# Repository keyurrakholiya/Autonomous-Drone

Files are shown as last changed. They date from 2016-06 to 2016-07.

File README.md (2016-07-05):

e-Yantra Summer Internship
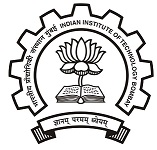
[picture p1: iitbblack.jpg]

***
# eYSIP-2016-Autonomous-Drone
Through this project we want to make an Autonomous Drone that can travel from one point to another based on its GPS Location. This drone can be used for tracking objects and aerial photography when interfaced with an Object Tracking Camera system.

Autonomous Drone project uses the following components:
* **Flight Controller:** Ardupilot Flight Controller (APM 2.6)
* **Copter Firmware:** v3.2.1
* **Communication Protocol:** MAVLink, MAVProxy, UART
* **Ground Station System (Software):** Mission Planner v1.3.30
* **Programming Language:** (Python 2.7)
* **Companion Computer:** Raspberry Pi B+ model

##Description:
***
The latest technology currently in markets is the Drone Technology, Drones can solve a lot of purposes such as security & surveillance, mapping unreachable or hard to reach sites, aerial photography, military purposes, forest survey, etc. So, we have created a drone which is completely autonomous as well as it can be manually controlled with laptop using remote login.

##Features:
***
- **Auto Take-off and Land:** The Drone can automatically take-off to a desired height, wait at that height for a predetermined time and then land.
- **Manual control using remote-login:** User can manually control the drone using the keyboard keystrokes of the laptop using remote login with raspberry pi.
- **Autonomous flight between multiple points:** The drone can autonomously take-off complete a mission and land either at the start position or your desired position. A mission is a set of locations where you want your drone to go. The drone gets the locations from the GPS module interfaced with the APM board.
- **Indoor auto take-off and land using ultrasonic sensor:** The drone also has an Ultrasonic sensor interfaced with Raspberry Pi which can be used for take-off and land indoors, where the altitude the drone needs to reach is just few meters.
- **Failsafe:** The APM has smart failsafe features which include low battery voltage failsafe, remote signal lost. So, with these failsafe features you can either put your drone into landing mode or else if you have a GPS module you can even have Return To Launch feature and also many more options are provided.

##Key Tasks
***
* Calculations for selecting motors, propellors, flight controller, battery for a Quadcopter
* Building and assembling the drone
* Stabilizing the drone for manual as well as autonomous control
* Interfacing Raspberry Pi with APM  flight controller
* Develop python codes to achive autonomous behaviour of drone

##Deliverables
***
* An Autonomous Drone
* Code and Documentation
* Tutorials explaining individual modules

##Documentation
***
* Detailed tutorials with actual component pictures on every module of the project have been uploaded on GitHub.

##Contributors
***
  * [Akshit Gandhi](https://github.com/akshitgandhi)
  * [Keyur Rakholiya](https://github.com/keyurrakholiya)
  
## Mentors
***
  * Pushkar Raj
  * Akshat Jain
  * Rama Kumar

##License
***
This project is open-sourced under [MIT License](http://opensource.org/licenses/MIT)

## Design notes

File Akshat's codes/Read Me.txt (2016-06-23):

These are the codes I used during my quadcopter project. 

Please do not attempt to run the codes directly as they will give errors. Make sure all the libraries used in the codes are installed on your device.

P.S.: Remove lines that are not relevant to you else it will give errors.

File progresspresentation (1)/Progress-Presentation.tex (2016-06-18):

\documentclass[10pt, a4paper]{beamer}

\usetheme{Berkeley}
\usecolortheme{sidebartab}

\documentclass{article}
\usepackage{graphicx}

\begin{document}
	\setbeamertemplate{sidebar left}{}
	\title{Progress Presentation-I}
	\subtitle{e-Yantra Summer Intership-2016 \\ $Autonomous-Drone$}
	\author{Akshit Gandhi\\Keyur Rakholiya\\
	Mentors:\\ Pushkar Raj\\Akshat Jain\\Rama Kumar}
	\institute{IIT Bombay}
	\date{\today}
	%\addtobeamertemplate{sidebar left}{}{\includegraphics[scale = 0.3]{logowithtext.png}}
	\frame{\titlepage}

\setbeamertemplate{sidebar left}[sidebar theme]
\section{Overview of Project}
\begin{frame}{Overview of Project}
	\textbf{Autonomous-Drone} \\
	\begin{itemize}
		\item Objective:\\
		            “Making an Autonomous Drone that can travel from one point to another based on its GPS Location. This drone can be used for tracking objects and aerial photography when interfaced with an Object Tracking Camera system.”

		\item Deliverables:\\
	1. An Autonomous Drone\\
2. Code and Documentation\\
3.Tutorials explaining individual modules

	\end{itemize}
\end{frame}

\section{Overview of Task}
\begin{frame}{Overview of Task}
\textbf{Task list}
 	\hspace{0.45in}\\
 	\begin{tabular}{|c|c|}
 		\hline
 		Task & Deadline &
 		\hline
 		Calculations for making a Quadcopter & 3/6/16 &
 		\hline
 		Calibrating APM & 5/6/16 &
 		\hline
 		Assembling the quad for manual flight & 7/6/16 &
 		\hline
 		Interface Gps with APM & 9/6/16 &
 		\hline
 		Interface Raspberry-Pi with APM & 11/6/16 &
 		\hline
 		Manual flight using R-pi & 15/6/16 &
 		\hline
 		Auto take-off and land using R-pi & 19/6/16 &
 		\hline
 		Create a flight planning algorithm & 25/6/16 &
 		\hline
 		Autonomous Flight & 3/7/16 &
 		\hline
\end{tabular}
\end{frame}

\section{Task Accomplished}
\begin{frame}{Task Accomplished}
	\begin{itemize}
	    \item Research on drone project.
		\item Assembly of drone.
		\item Understanding software and Flight controller features.
		\item Interface GPS.
		\item TEST FLIGHT-1 done.
		\item Research on dronekit Library version.
		\item Installing Rasbarian linux on R pi.
		\item connect R-pi to Ardupilot via USART or USB
		\item Run python code on R pi to get data from Flight controller.
	\end{itemize}
\end{frame}

\begin{frame}{Images}
	Quadcopter with Mission planer software: \\
	\centering
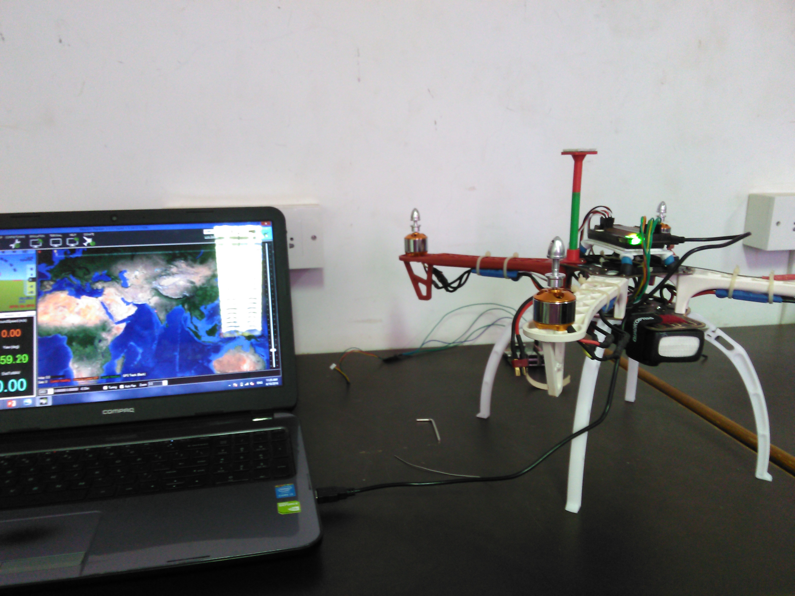
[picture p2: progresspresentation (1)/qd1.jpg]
		

\end{frame}

\begin{frame}{Images}
	Ardupilot Flight Controller: \\
	    \centering
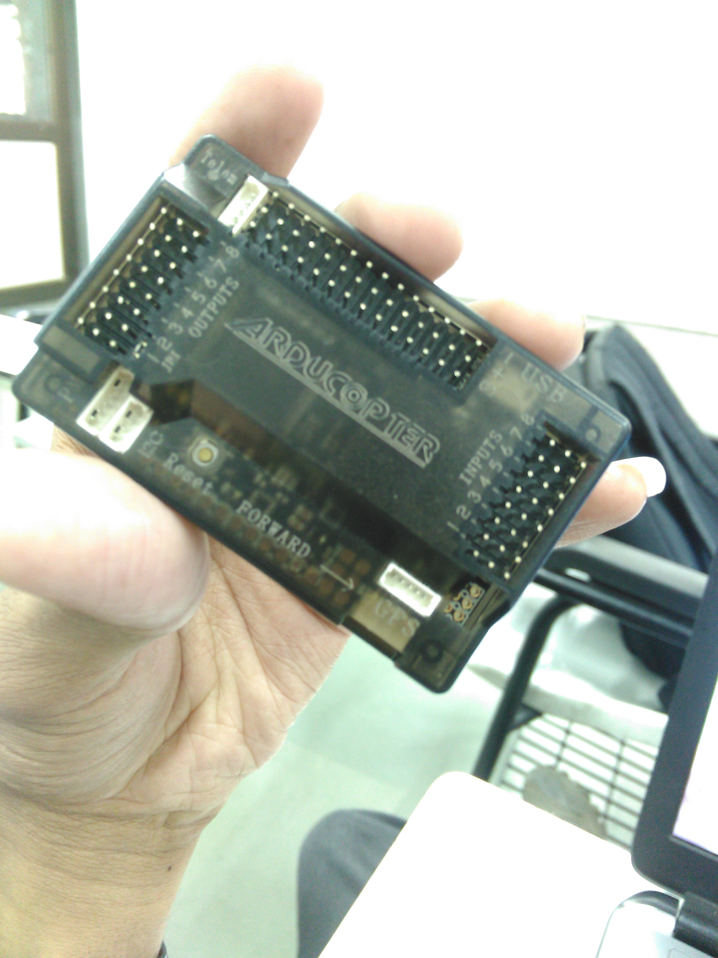
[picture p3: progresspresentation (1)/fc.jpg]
		
\end{frame}

\section{Challenges Faced}
\begin{frame}{Challenges Faced}
     \large\textbf{Hardware challenges}
	\begin{itemize}
	    \item Calculation of total approx weight.
	    \item For lifting the drone, calculate the thrust
	    \item knowing the aerodynamics rules
	    \item Choose the right propellers in size and pitch
	    \item Calculate flight time
	    \item BLDC motor power rating and KVA rating
	    \item Choose right battery 
	    \item Carbon fiber frame for drone
	    \inem Interfacing sensors Like GPS,SONAR
	    
	\end{itemize}
\end{frame}

\section{Challenges Faced}
\begin{frame}{Challenges Faced}
     \large\textbf{Software challenges}
	\begin{itemize}
	    \item Ardupilot is open source Hardware.They release new version after fixing bugs! its very difficult to choose right firmware  for your hardware among hundreds of software
	    \item Finding out suitable version of MISSION PLANNER for your firmware
	    \item More then 239 parameters are there. according to our mission we have to make changes
		\item Calibration axis of gyro and radio channels.
	\end{itemize}
\end{frame}

\section{Future Plans}
\begin{frame}{Future Plans}
	\begin{itemize}
	    
		\item Writing code in python 
		\item Making drone autonomous\\
		By Autonomous, we mean that drone will fly and reach to our desire destination without Remote control.
		\item Mounting camera on drone , and making it object tracking drone
	\end{itemize}
\end{frame}

\section{Thank You}
\begin{frame}{Thank You}
	\centering THANK YOU !!!
\end{frame}
\end{document}

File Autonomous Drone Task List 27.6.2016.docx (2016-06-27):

eYSIP – 2016

Autonomous Drone

Completed, Under Review and Upcoming Tasks as of 27/6/2016

Completed:

1. Calculations for deciding the components to be used for drone.
2. Assembly of Drone.
3. Calibrating APM.
4. First Manual Test Flight
5. Interfacing GPS with APM and reading values from it.
6. Interfacing Ultrasonic Sensor with APM and reading values from it.
7. Setting up the Raspberry Pi.
8. Create a Power distribution system for the drone, RPi and APM.
9. Interfacing the Raspberry Pi with APM.
10. Manual flight using Raspberry Pi (remote login). No need to prepare a tutorial for this but the code should be well commented.
11. Auto take-off and landing using Raspberry Pi.

Under Review:

1. Preparing a tutorial on “How to decide what parts to use for building a quadcopter?”
2. Tutorial on “Setting up your APM, calibrating all devices”.
3. Prepare a tutorial on interfacing the GPS with APM.
4. Prepare a tutorial on Power distribution system.
5. Prepare a tutorial on interfacing the Raspberry Pi with APM.

Upcoming:

6. Prepare a tutorial on interfacing the Ultrasonic Sensor with APM.
7. Commenting the “Manual flight using Raspberry Pi” code.
8. Commenting the “Auto take-off and landing using Raspberry Pi” code.
9. Designing of Path Planning Algorithm to travel from one GPS location to another. Prepare a tutorial for the same.
10. First Completely Autonomous Test Flight.
11. Debugging.
12. Adding features. Prepare tutorials if required.

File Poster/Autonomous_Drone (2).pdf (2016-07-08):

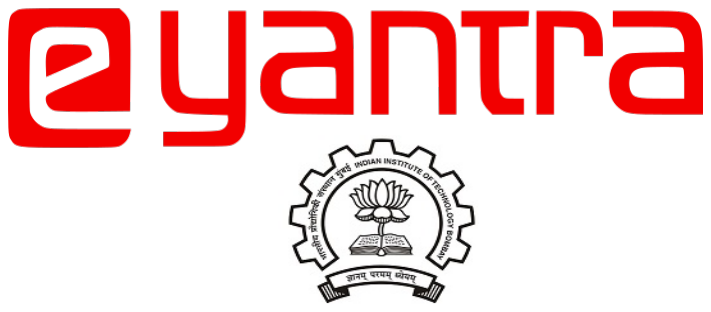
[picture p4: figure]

# Autonomous-Drone

Akshit Gandhi, Keyur Rakholiya. Mentors: Pushkar Raj,
Rama Kumar,
Akshat Jain.

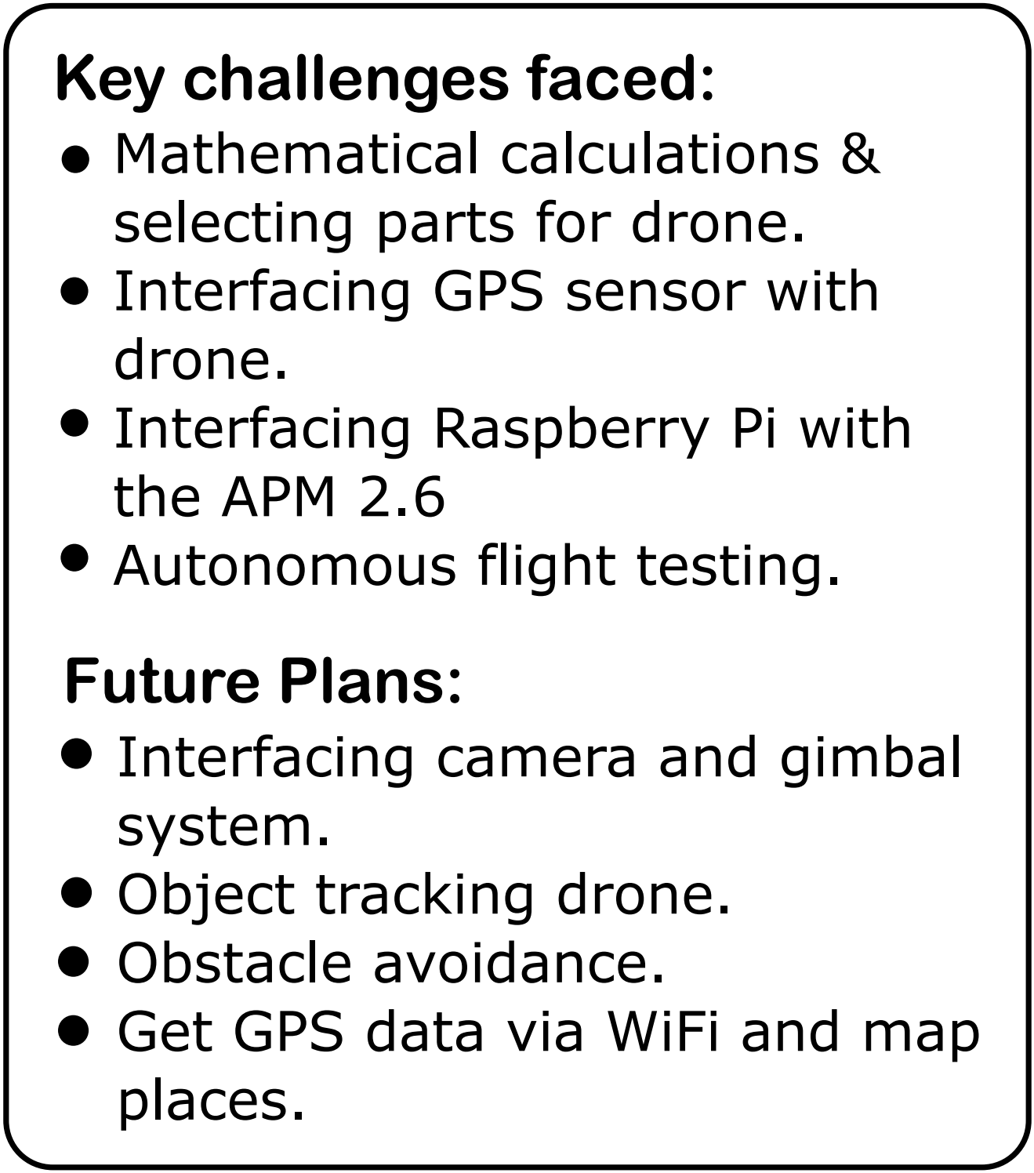
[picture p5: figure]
Key challenges faced: Mathematical calculations & selecting parts for drone. Interfacing GPS sensor with drone. Interfacing Raspberry Pi with the APM 2.6 Autonomous flight testing.; Future Plans: Interfacing camera and gimbal system. Object tracking drone. Obstacle avoidance. Get GPS data via WiFi and map places.
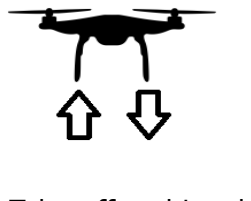
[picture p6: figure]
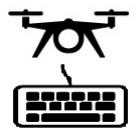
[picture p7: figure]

### e-Yantra Summer Internship Project 2016

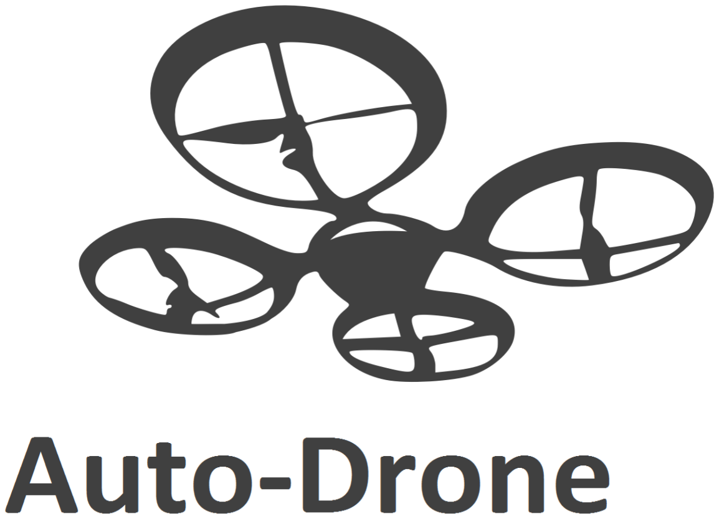
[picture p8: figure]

The latest innovation in the aviation industry is the Drone Technology.

### But, the drones that require manual input are very susceptible to radio inter-

ference or radio connection losses and they also have very limited features.

### So, we came up with a solution i.e the Autonomous-Drone

### Key Features:

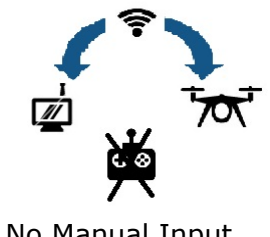
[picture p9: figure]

No Manual Input | Auto Take-off and Land | Control from keyboard

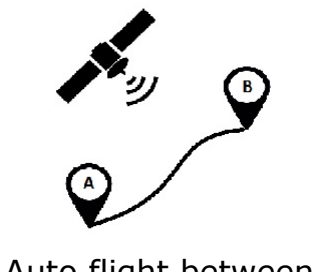
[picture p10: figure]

Auto flight between
multiple way-points

Indoor Take-off and land
with ultrasonic-sensor

Application fields include security surveillance, perimeter defence, mapping hard to reach sites, aerial photography, forest surveys, just to name a few!!

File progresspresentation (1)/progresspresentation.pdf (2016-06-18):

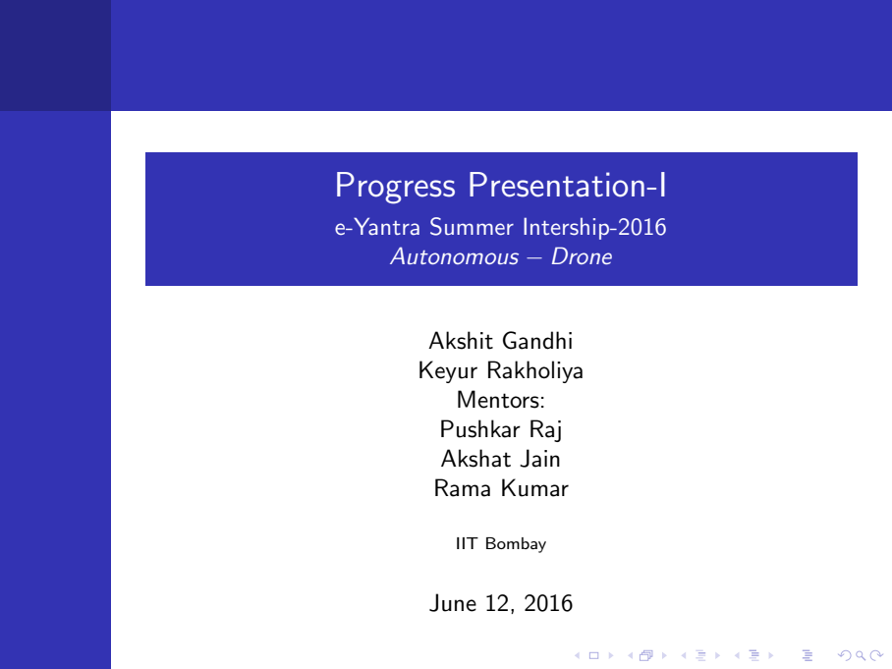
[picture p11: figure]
Progress Presentation-I; e-Yantra Summer Intership-2016 Autonomous − Drone; Akshit Gandhi Keyur Rakholiya Mentors: Pushkar Raj Akshat Jain Rama Kumar; IIT Bombay; June 12, 2016

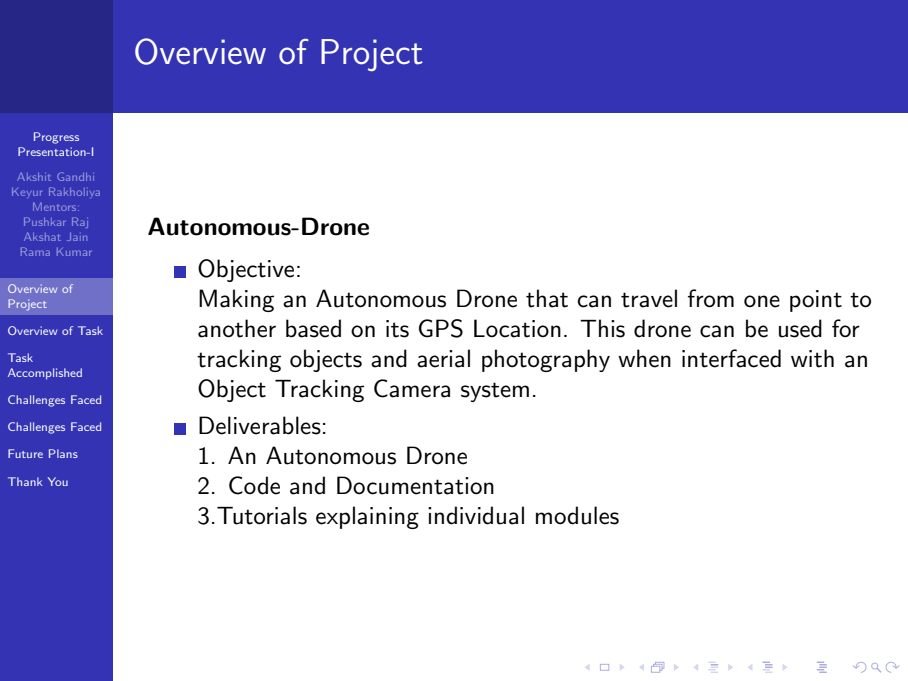
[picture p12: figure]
Progress Presentation-I; Akshit Gandhi Keyur Rakholiya Mentors: Pushkar Raj Akshat Jain Rama Kumar; Overview of Project; Overview of Task; Task Accomplished; Challenges Faced; Future Plans; Thank You; Autonomous-Drone; Objective:; Object Tracking Camera system.; Deliverables: 1. An Autonomous Drone 2. Code and Documentation

# Making an Autonomous Drone that can travel from one point to another based on its GPS Location. This drone can be used for tracking objects and aerial photography when interfaced with an

# 3.Tutorials explaining individual modules

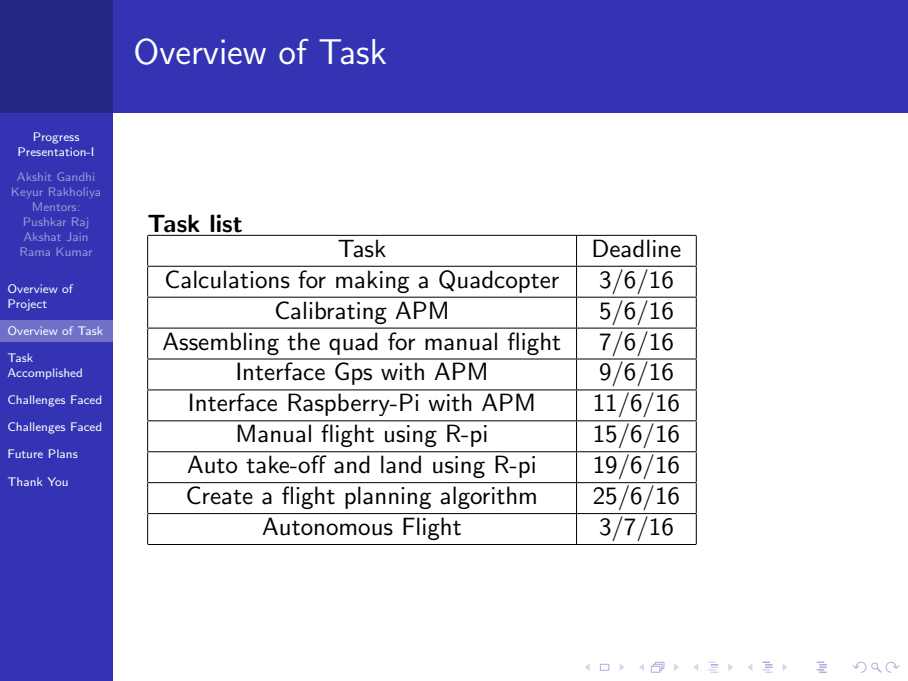
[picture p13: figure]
Progress Presentation-I; Akshit Gandhi Keyur Rakholiya Mentors: Pushkar Raj Akshat Jain Rama Kumar; Overview of Project; Overview of Task; Task Accomplished; Challenges Faced; Future Plans; Thank You; Task list; Task; Deadline; Calibrating APM; Interface Gps with APM; Interface Raspberry-Pi with APM; Manual flight using R-pi; Autonomous Flight

Calculations for making a Quadcopter | 3/6/16
Assembling the quad for manual flight | 7/6/16
Auto take-off and land using R-pi | 19/6/16
Create a flight planning algorithm | 25/6/16

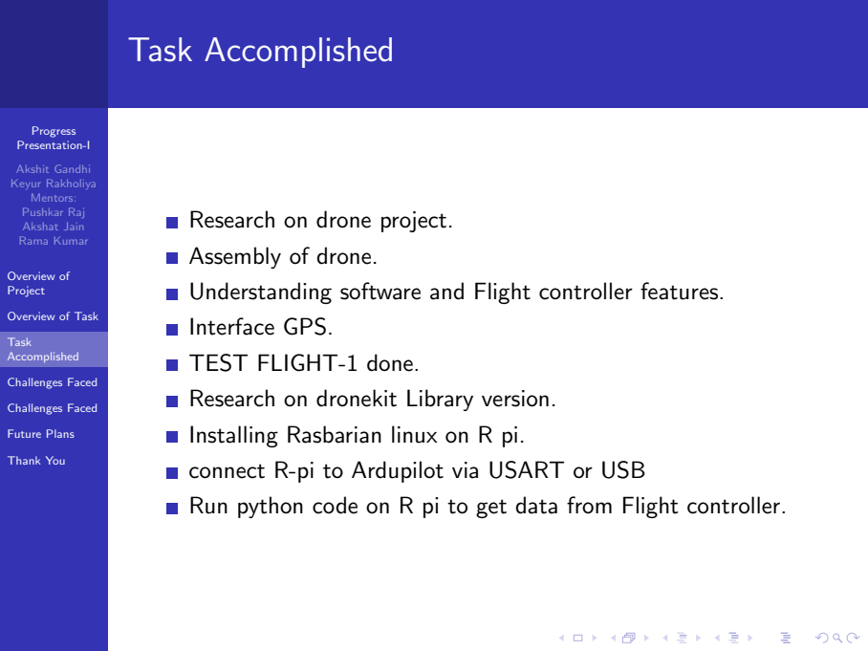
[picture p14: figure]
Progress Presentation-I; Akshit Gandhi Keyur Rakholiya Mentors: Pushkar Raj Akshat Jain Rama Kumar; Overview of Project; Overview of Task; Task Accomplished; Challenges Faced; Future Plans; Thank You; Research on drone project.; Assembly of drone.; Interface GPS.; TEST FLIGHT-1 done.; Research on dronekit Library version.; Installing Rasbarian linux on R pi.

Understanding software and Flight controller features.

# connect R-pi to Ardupilot via USART or USB

Run python code on R pi to get data from Flight controller.

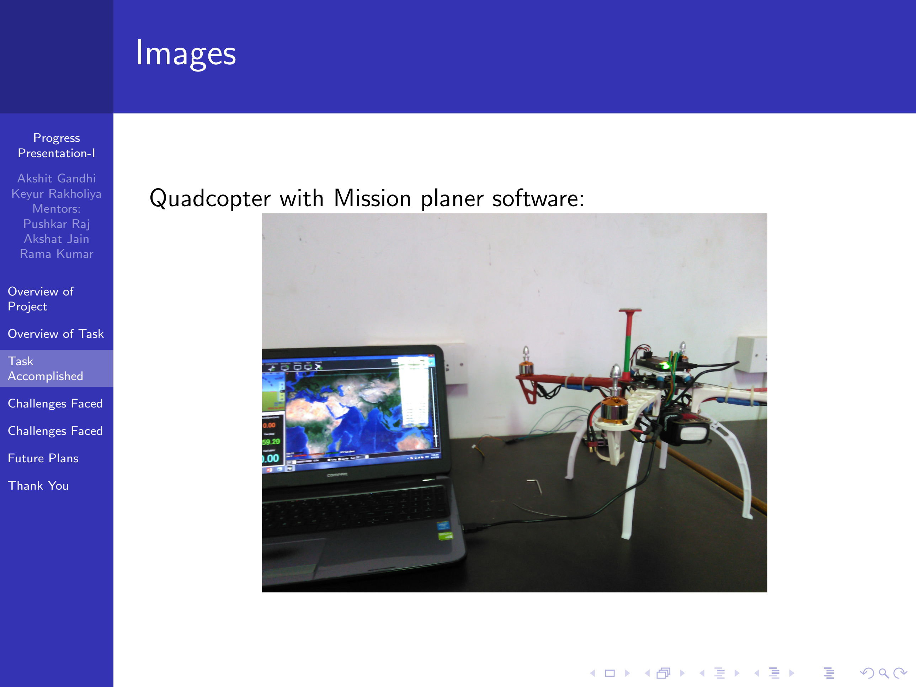
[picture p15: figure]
Progress Presentation-I; Akshit Gandhi Keyur Rakholiya Mentors: Pushkar Raj Akshat Jain Rama Kumar; Overview of Project; Overview of Task; Task Accomplished; Challenges Faced; Future Plans; Thank You; Images

# Quadcopter with Mission planer software:

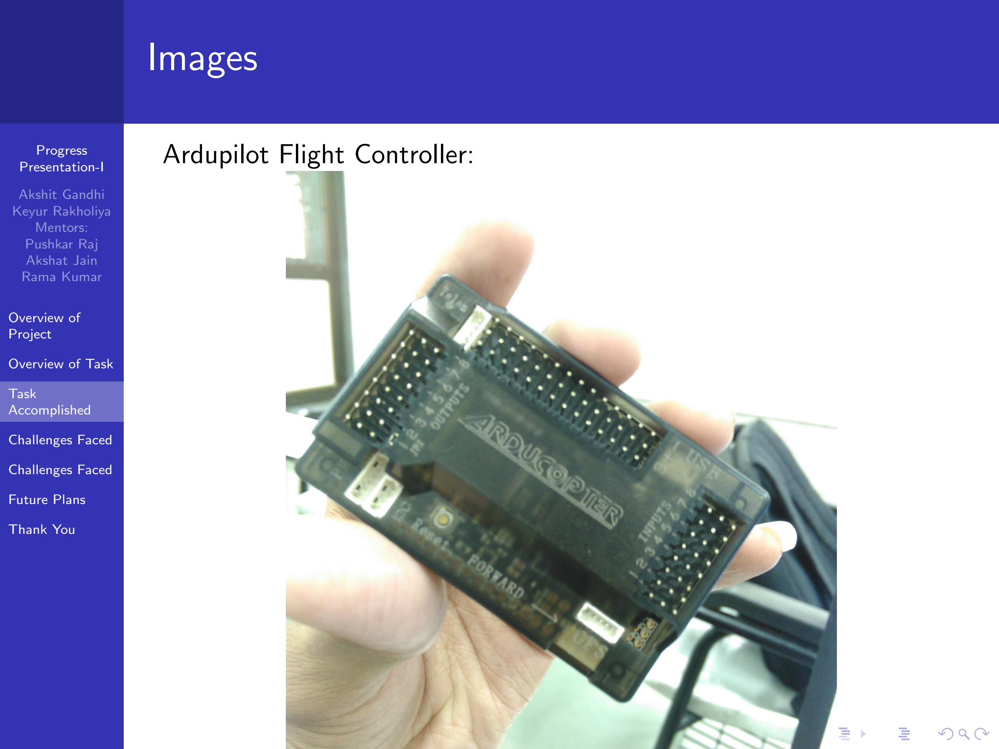
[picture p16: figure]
Progress Presentation-I; Akshit Gandhi Keyur Rakholiya Mentors: Pushkar Raj Akshat Jain Rama Kumar; Overview of Project; Overview of Task; Task Accomplished; Challenges Faced; Future Plans; Thank You; Images; Ardupilot Flight Controller:

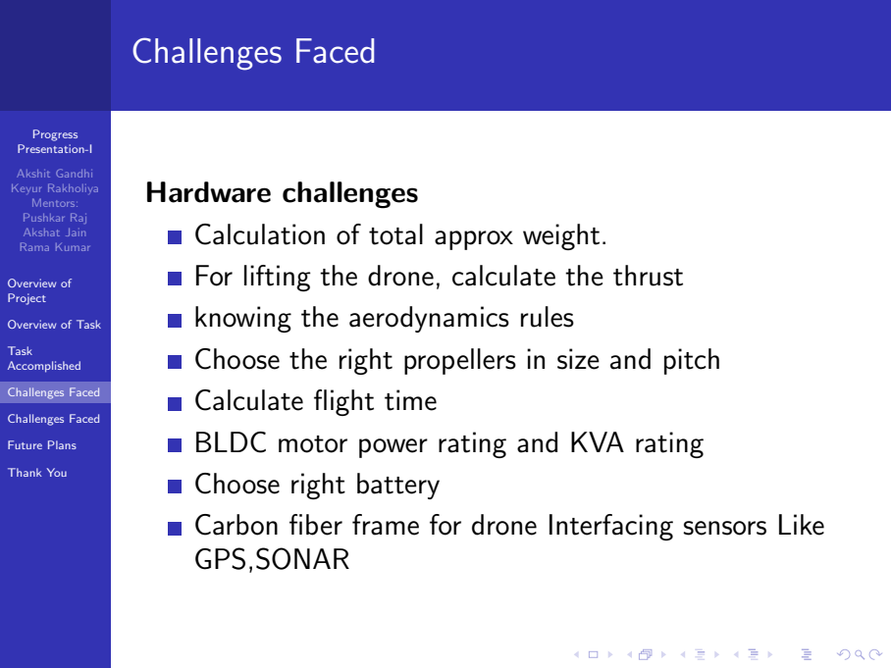
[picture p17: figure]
Progress Presentation-I; Akshit Gandhi Keyur Rakholiya Mentors: Pushkar Raj Akshat Jain Rama Kumar; Overview of Project; Overview of Task; Task Accomplished; Challenges Faced; Future Plans; Thank You; Hardware challenges; Calculation of total approx weight.; knowing the aerodynamics rules; Calculate flight time; BLDC motor power rating and KVA rating; Choose right battery; GPS,SONAR

# For lifting the drone, calculate the thrust

# Choose the right propellers in size and pitch

# Carbon fiber frame for drone Interfacing sensors Like

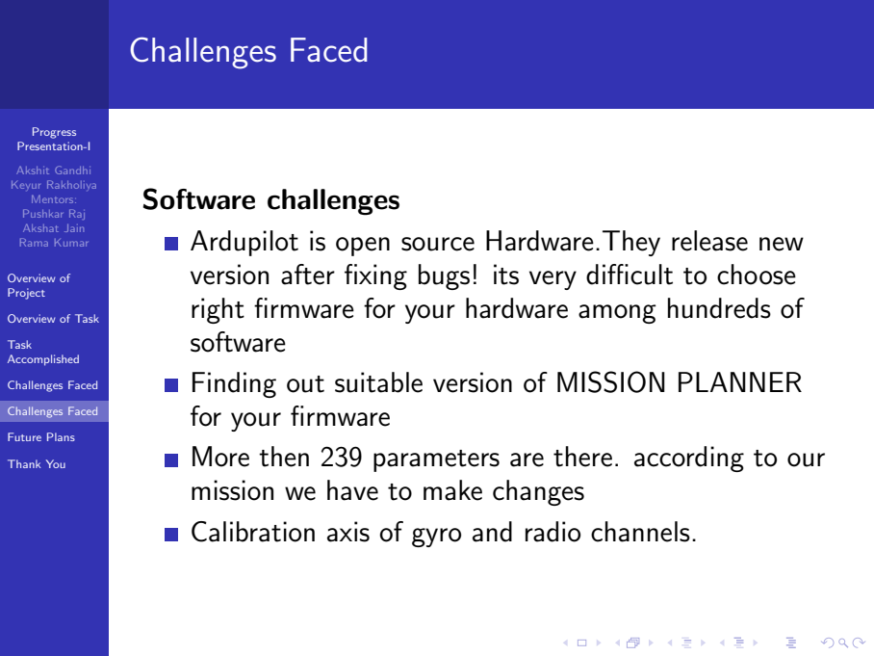
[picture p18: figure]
Progress Presentation-I; Akshit Gandhi Keyur Rakholiya Mentors: Pushkar Raj Akshat Jain Rama Kumar; Overview of Project; Overview of Task; Task Accomplished; Challenges Faced; Future Plans; Thank You; Software challenges; software; for your firmware; mission we have to make changes

# Ardupilot is open source Hardware.They release new version after fixing bugs! its very difficult to choose right firmware for your hardware among hundreds of

# Finding out suitable version of MISSION PLANNER

# More then 239 parameters are there. according to our

Calibration axis of gyro and radio channels.

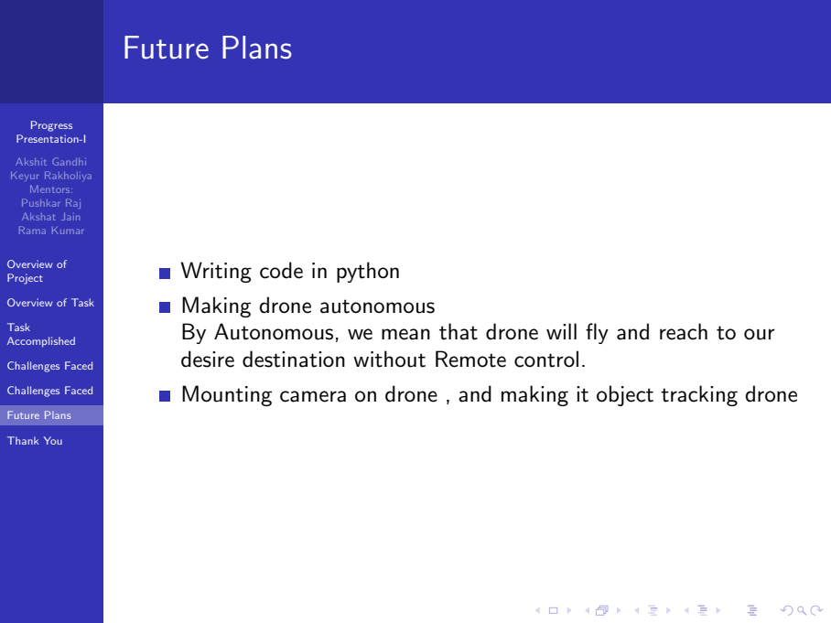
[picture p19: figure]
Progress Presentation-I; Akshit Gandhi Keyur Rakholiya Mentors: Pushkar Raj Akshat Jain Rama Kumar; Overview of Project; Overview of Task; Task Accomplished; Challenges Faced; Future Plans; Thank You; Writing code in python; Making drone autonomous

# By Autonomous, we mean that drone will fly and reach to our

desire destination without Remote control.

# Mounting camera on drone , and making it object tracking drone

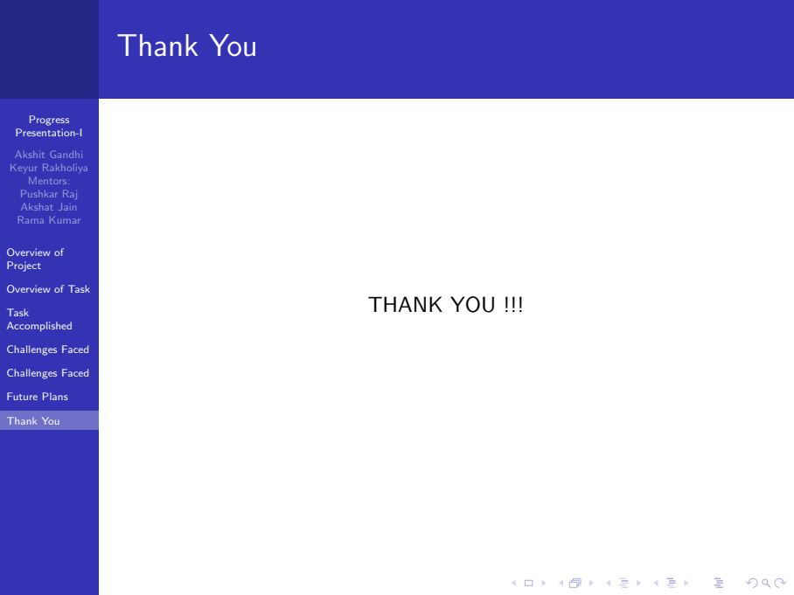
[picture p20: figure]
Progress Presentation-I; Akshit Gandhi Keyur Rakholiya Mentors: Pushkar Raj Akshat Jain Rama Kumar; Overview of Project; Overview of Task; Task Accomplished; Challenges Faced; Future Plans; Thank You; THANK YOU !!!

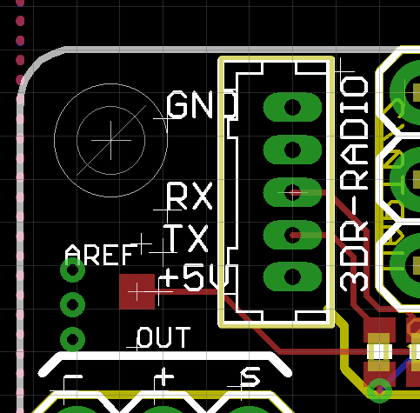
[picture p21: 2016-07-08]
report/Picture1.png

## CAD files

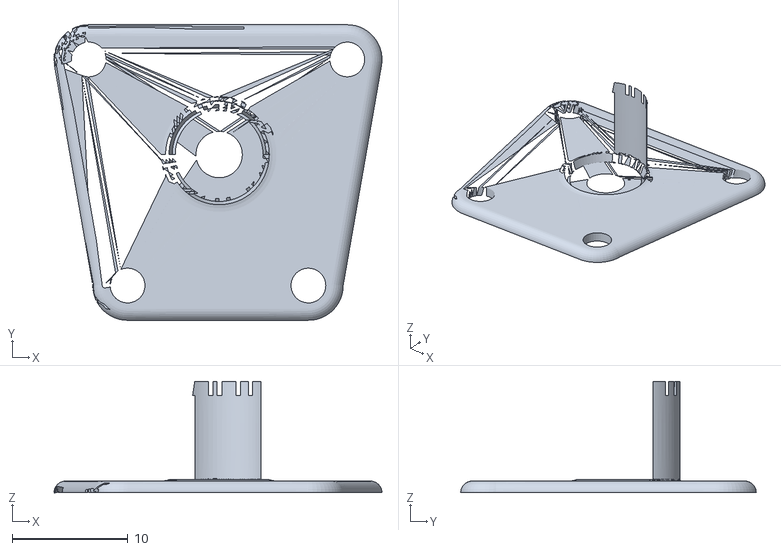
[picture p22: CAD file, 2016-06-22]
3D printing/Flamewheel_Arm_GPS_Mast_Holder/Untitled-57569d04.stl
28.3 x 25.5 x 9.60

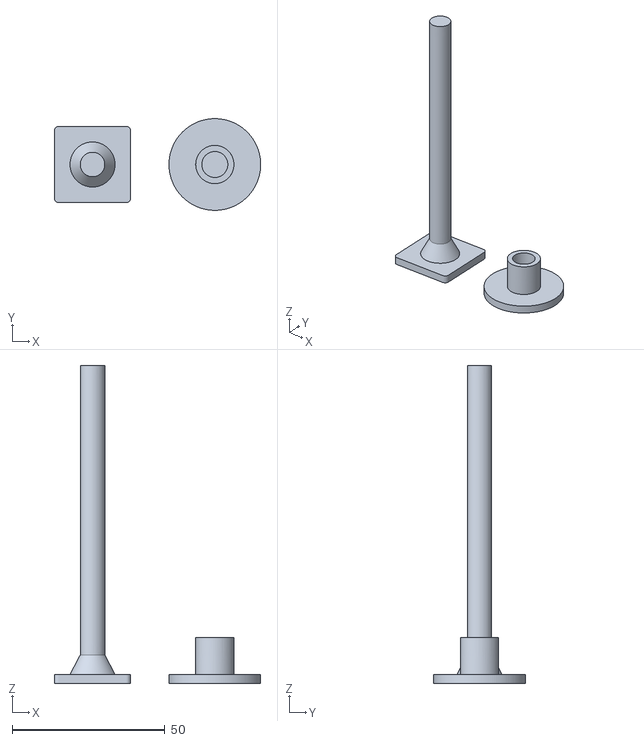
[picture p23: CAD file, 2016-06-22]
3D printing/GPSCompass_Stand_for_APM_and_Pixhawk_Multirotors/GPSCompass_Stand_for_APM_and_Pixhawk_Multirotors/apm_pixhawk_gps_compass_stand.stl
67.5 x 30.0 x 104.0

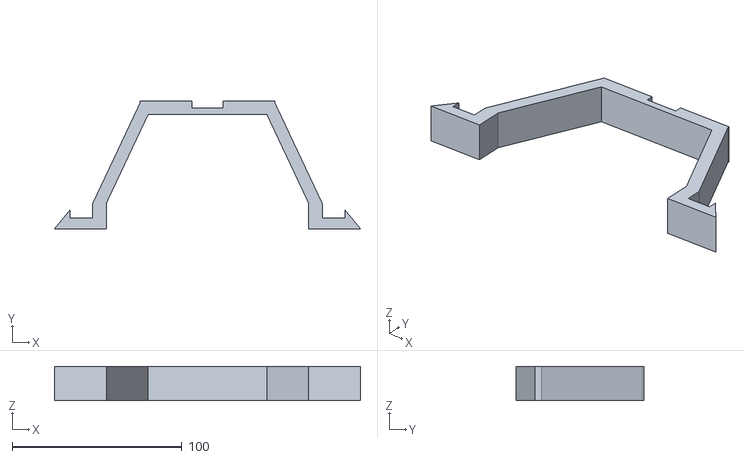
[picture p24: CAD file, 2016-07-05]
3D printing/Quad_Cage_Akshit/part2.stl
180.0 x 75.0 x 20.0

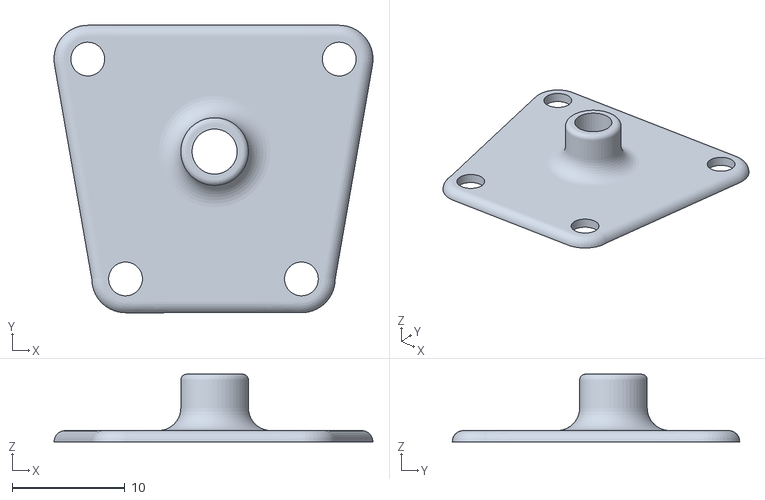
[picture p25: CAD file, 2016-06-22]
3D printing/Flamewheel_Arm_GPS_Mast_Holder/Flamewheel_Arm_GPS_MastHolder.stl
28.3 x 25.5 x 6.00

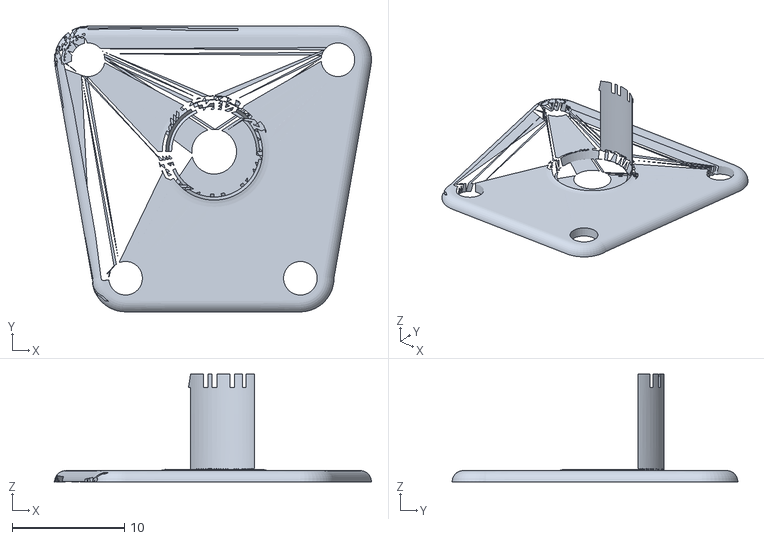
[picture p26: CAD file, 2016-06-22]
3D printing/Flamewheel_Arm_GPS_Mast_Holder/Untitled-57569ca1.stl
28.3 x 25.5 x 9.60

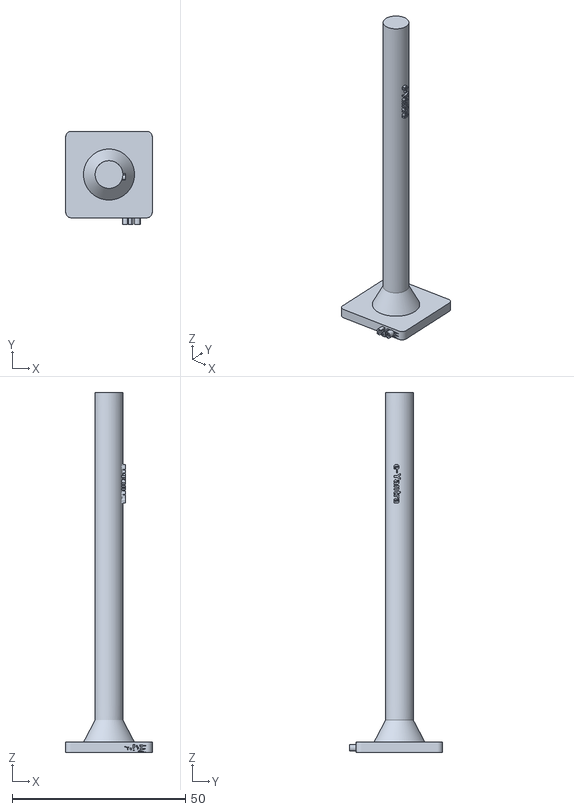
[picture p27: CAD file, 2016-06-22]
3D printing/Flamewheel_Arm_GPS_Mast_Holder/2.stl
25.0 x 27.0 x 104.0

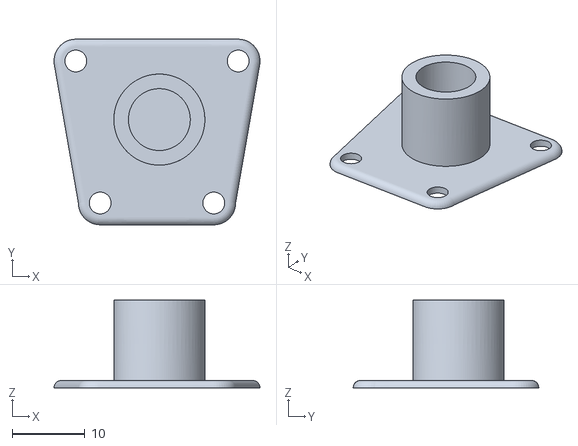
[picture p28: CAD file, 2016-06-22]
3D printing/Flamewheel_Arm_GPS_Mast_Holder/1.stl
28.3 x 25.5 x 12.0

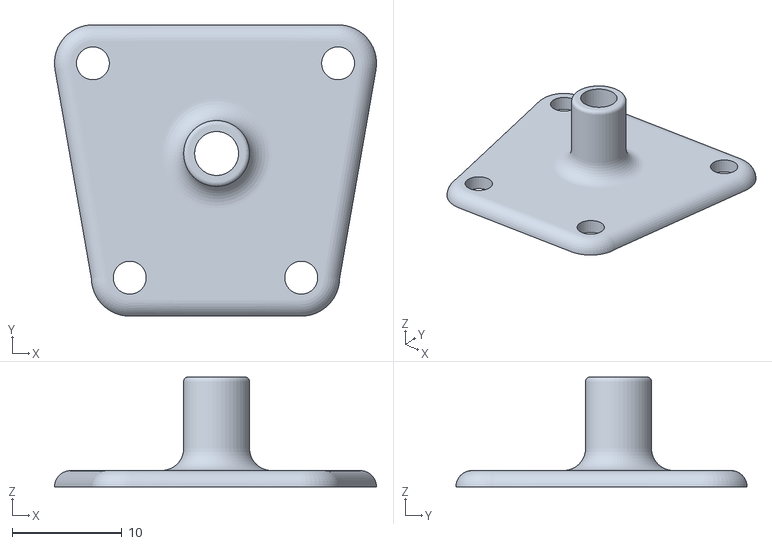
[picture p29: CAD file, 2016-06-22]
3D printing/Flamewheel_Arm_GPS_Mast_Holder/Flamewheel_Arm_GPS_MastHolderV2.stl
29.3 x 26.5 x 10.0

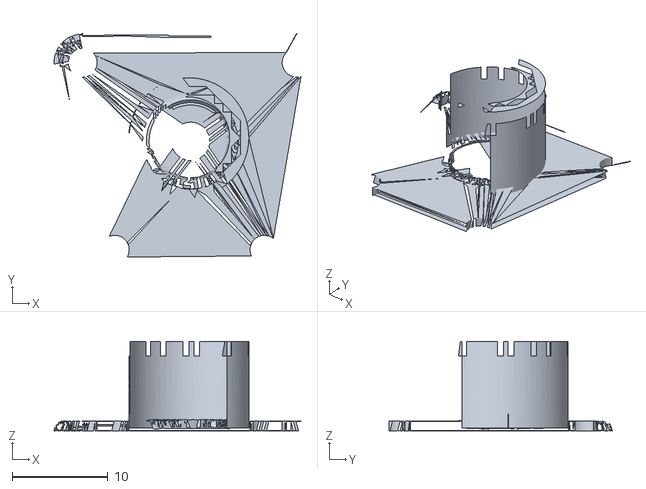
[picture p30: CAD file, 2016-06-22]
3D printing/Flamewheel_Arm_GPS_Mast_Holder/Untitled-57569d55.stl
25.8 x 23.3 x 10.8

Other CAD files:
3D printing/Quad_Cage_Akshit/part1.stl

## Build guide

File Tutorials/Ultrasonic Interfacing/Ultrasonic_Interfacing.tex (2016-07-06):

%%%%%%%%%%%%%%%%%%%%%%%%%%%%%%%%%%%%%%%%%%%%%%%%%%%%%%%%%%%%%%%%%%%%%%%%%%%%%
%	e-Yantra, IIT-Bombay

%	Document Author: Saurav Shandilya
%	Date: 16-August,2012
%	Last Editted by: Saurav
%   Date Last updated: 31-05-2016 

%%%%%%%%%%%%%%%%%%%%%%%%%%%%%%%%%%%%%%%%%%%%%%%%%%%%%%%%%%%%%%%%%%%%%%%%%%%%%

\documentclass[11pt,a4paper]{article}

\usepackage{graphicx}
\usepackage{float}
\usepackage{hyperref}
\title{Interface Ultrasonic Sensor with R-Pi}
\author{Akshit Gandhi \\ Keyur Rakholiya}
\date{\today}

\begin{document}
	\maketitle
	\newpage
	\tableofcontents
	\newpage
	\section{Tutorial Name}
		Interfacing Ultrasonic sensor with Raspberry Pi.
		\paragraph{•}
		\textbf{Objective}
		\paragraph{}In this tutorial we will be going through on how to interface an ultrasonic sensor with R-Pi. The Ultrasonic Sensor which we will be using is the HC-SR04. The HC-SR04 sensor cannot be directly used with the R-Pi, we need a voltage divider circuit, the reason will be explained in the later sections.
		\paragraph{•}The reason for using ultrasonic sensor with the quadcopter setup is that, when flying indoors autonomously we need some sort of sensor that will provide the altitude details of the quadcopter, we know that the APM 2.6 has the \textbf{Barometer Sensor}, but the limitation is that it is accurate only above 5 meters height (altitude). So, we need an Ultrasonic Sensor for height (altitude) measurement.
		\paragraph{•}We also tried interfacing the \textbf{Sonar Sensor} which is compatible with the APM 2.6. The Sonar we used is the [Maxbotic Sonar MB-1200 series]. But it didn't give us the desired results. So, we moved onto using the HC-SR04.
	\section{Prerequisites}
		Knowledge of voltage divider circuit.
	\section{Hardware Requirement}
		R-Pi, wires, HC-SR04 sensor, 1000 Ohm and 680 Ohm resistances (1 each)
	\section{Theory and Description}
		\subsection{Connecting to R-Pi}
			Powering the module is easy. Just connect the +5V and Ground pins to Pin 2 and GPIO21 on the Pi’s GPIO header.
			\begin{figure}[h]
				\centering
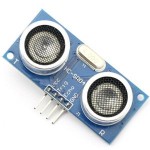
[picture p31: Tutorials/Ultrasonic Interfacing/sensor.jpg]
				
				\caption{HC-SR04 Sensor}
			\end{figure}

\paragraph{}The input pin on the module is called the “trigger” as it is used to trigger the sending of the ultrasonic pulse. Ideally it wants a 5V signal but it works just fine with a 3.3V signal from the GPIO. So we connected the trigger directly to GPIO20 on our GPIO header.
\paragraph{}
You can use any GPIO pins you like on your RPi but you will need to note the references and amend your Python script accordingly.
\paragraph{•}
The module’s output is called the “echo” and needs a bit more thought. The output pin is low (0V) until the module has taken its distance measurement. It then sets this pin high (+5V) for the same amount of time that it took the pulse to return. So our script needs to measure the time this pin stays high. The module uses a +5V level for a “high” but this is too high for the inputs on the GPIO header which only like 3.3V. In order to ensure the Pi only gets hit with 3.3V we can use a basic voltage divider. This is formed with two resistors.
\paragraph{•}
If R1 and R2 are the same then the voltage is split in half. This would give us 2.5V. If R2 is twice the value of R1 then we get 3.33V which is fine. So ideally you want R2 to be between R1 and R1 x 2. But we used 1000 and 680 ohm resistors (Because it worked the best for us!).
\paragraph{•}
Here is a diagram of our final circuit. We chose GPIO20 and GPIO16 [echo], but you can use any of the available GPIO pins on the GPIO header. Just remember to update the script.
	\begin{figure}[H]
	 	\centering
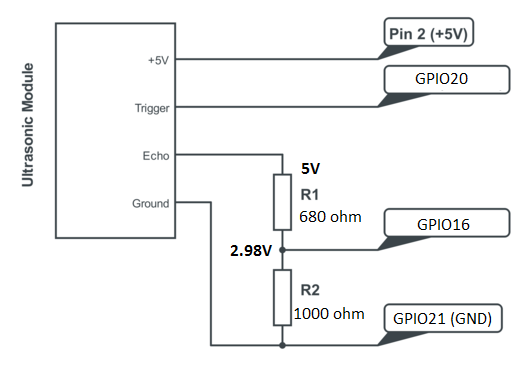
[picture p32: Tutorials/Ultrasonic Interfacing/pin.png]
		
		\caption{Circuit Diagram}
	\end{figure}
	\subsection{Python Script}
		Once you have followed above connection diagram you can test the sensor you are ready with the next part i.e to access the sensor values using the python script. The script is in the codes folder.
	\subsection{Accuracy}
		\begin{itemize}
			\item The accuracy of the distance measurement is dependent on timing. Python under Linux is not ideal for precise timing but for general messing about it will work OK. To improve accuracy you would need to start looking at using C instead.
			\item When the GPIOs are configured the module needs some time before it is ready to take its first reading so we added a 0.5 second delay to the start of the script.
			\item The transducers have a wide angle of sensitivity. In a cluttered environment you may get shorter readings due to objects to the side of the module.
			\item Measurements work down to about 2cm. Below this limit the results can give strange results.
			\item If the ultrasonic transducers touch anything the results are unpredictable.
		\end{itemize}
	\section{References}
		For more understanding you can visit the below two sites:\\
			\url{http://www.raspberrypi-spy.co.uk/2012/12/ultrasonic-distance-measurement-using-python-part-1/}\\
			\url{http://www.modmypi.com/blog/hc-sr04-ultrasonic-range-sensor-on-the-raspberry-pi}
	
\end{document}

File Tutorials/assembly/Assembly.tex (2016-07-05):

 %%%%%%%%%%%%%%%%%%%%%%%%%%%%%%%%%%%%%%%%%%%%%%%%%%%%%%%%%%%%%%%%%%%%%%%%%%%%%
%	e-Yantra, IIT-Bombay

%	Document Author: Akshit Gandhi
%	Date: 7-June,2016
%	Last Editted by: Akshit
%   Date Last updated: 6-07-2016 

%%%%%%%%%%%%%%%%%%%%%%%%%%%%%%%%%%%%%%%%%%%%%%%%%%%%%%%%%%%%%%%%%%%%%%%%%%%%%

\documentclass[11pt,a4paper]{article}
\usepackage{float}
\usepackage{graphicx}
\usepackage{hyperref}
\title{Assembling The Quadcopter}
\author{Keyur Rakholiya \\ Akshit Gandhi}
\date{\today}

\begin{document}
	\maketitle
	\newpage
	\tableofcontents
	\newpage
	\section{Objective}
	Topic: Assembling the quadcopter
		In this tutorial we will study about the assembling of the quadcopter.
	\section{Prerequisites}
	refer the previous tutorial first.
	1. calculation
	
	choose your flight controller, motors,propellers,frame,battery.
	\section{Hardware Requirement}
	 All the components mentioned previously and a Soldering kit, deans connector and wires, M3*8 screws.
	\section{Assembly}
	 So, now we start with the assembly of the quad, ensure you have all the components mentioned previously.
	 \subsection{Assembling the Motors}
	 	Once you get the motors, the very first job is to mount the motors on the F450 frame. For this you will need M3 screws, so with the help of a screw-driver or L-key mount the motors on the arm of the quad like this:
	 	\begin{figure}[h]
	 	
	 	\centering
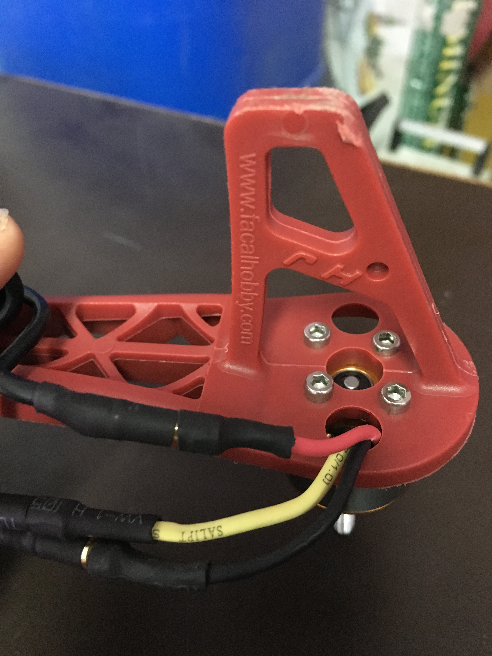
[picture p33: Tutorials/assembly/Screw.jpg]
		
		\caption{installing motors}
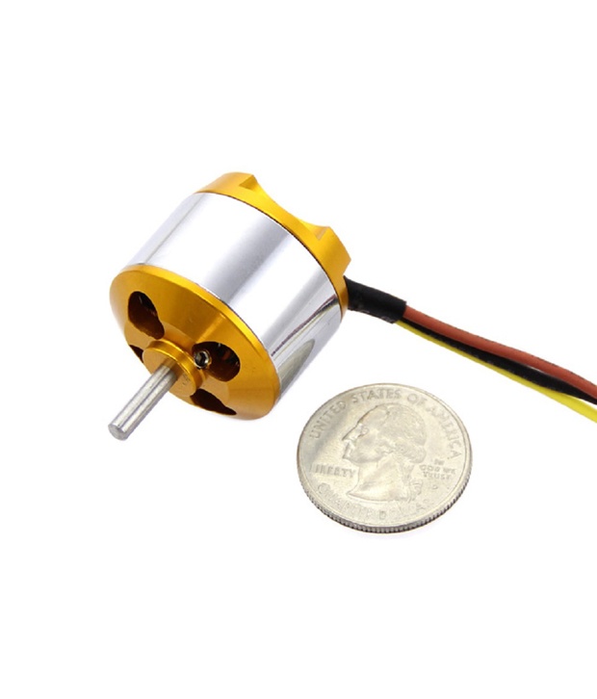
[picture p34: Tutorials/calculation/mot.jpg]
	 	
	 	\caption{Motor Assembly.}
\end{figure}
	 	\subsection{Esc mount}
	 	After the motors have been attached on the arms, next job is to attach the esc's, you can tie individual esc's on the arms using cable ties as shown below.
		 	
	 	 Also connect 3 wires from the esc's to the 3 wires on the motor, don't worry about the order in which the wires have to be connected we will look upon that in later tutorials.on ce your arms are ready with the escs and motors it will look something like this:
	 	 \begin{figure}[h]
	 	
	 	\centering
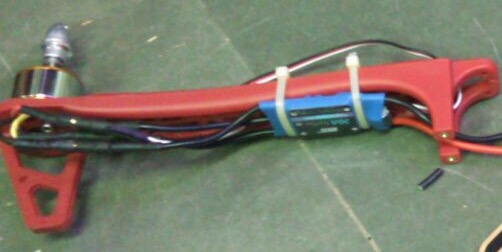
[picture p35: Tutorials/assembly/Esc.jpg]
		
		\caption{Esc Assembly.}
		\end{figure}
		
		\subsection{Connecting Esc to Power distribution board}
		The F450 frame comes with an inbuilt power distribution board so you just need to solder the esc wires (both positive and ground) to the pcb on the base plate. The pcb would look something like this.
		\begin{figure}[h]
	 	
	 	\centering
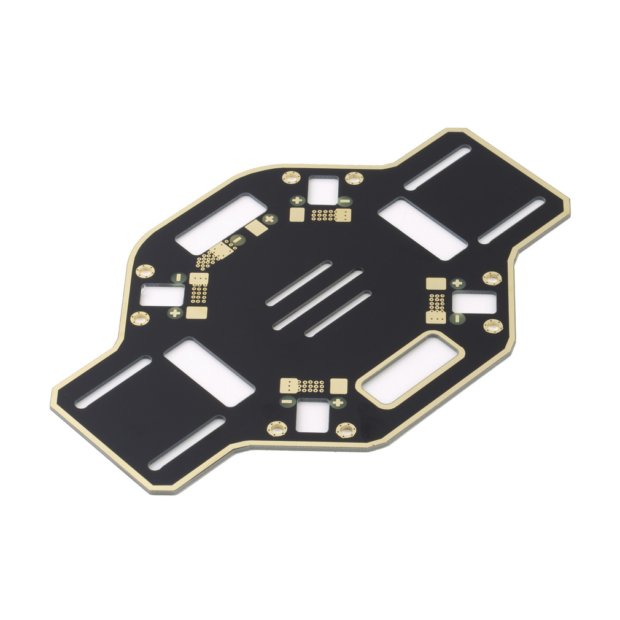
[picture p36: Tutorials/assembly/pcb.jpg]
		
		\caption{Power distribution Board.}
		\end{figure}
		
You will see that there are some points to attach the esc's marked as + or - and also on extra pair of points will be there for connecting the battery to the distribution board. First you need to ensure that there are no connectors on the esc( on the +ve and -ve wires), if there are any connectors desolder them and then solder the wires onto the pcb. Special care to ensure that +ve wires is soldered onto the +ve of the pcb and respectively for negative. Once you have soldered the wires onto the assembly would look something like this:
		\begin{figure}[h]
	 	
	 	\centering
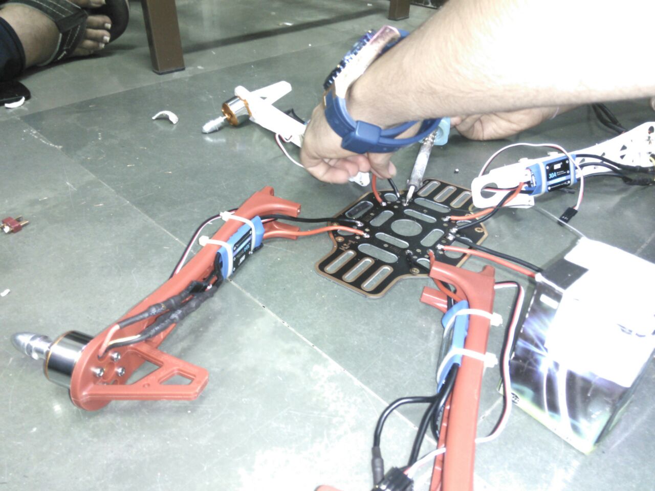
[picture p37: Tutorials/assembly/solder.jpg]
		
		\caption{Soldering.}
		\end{figure}
		
		\begin{figure}[h]
	 	
	 	\centering
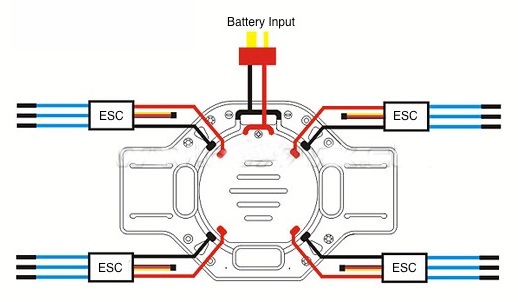
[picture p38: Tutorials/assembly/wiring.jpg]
		
		\caption{Wiring Schematic.}
		\end{figure}
		
		\subsection{Putting the frame together}
		Now you have your frame ready the next step is to use the screws provided with the kit to mount the arms on the lower plate and after that attach the upper plate. After this step your quad should look like this:
		\paragraph{}But an IMPORTANT note: To make it easy for you to know the orientation of the quad you can setup the frame in such a way that 2 adjacent white/red arms point to the forward direction of the quad.
		\begin{figure}[h]
	 	
	 	\centering
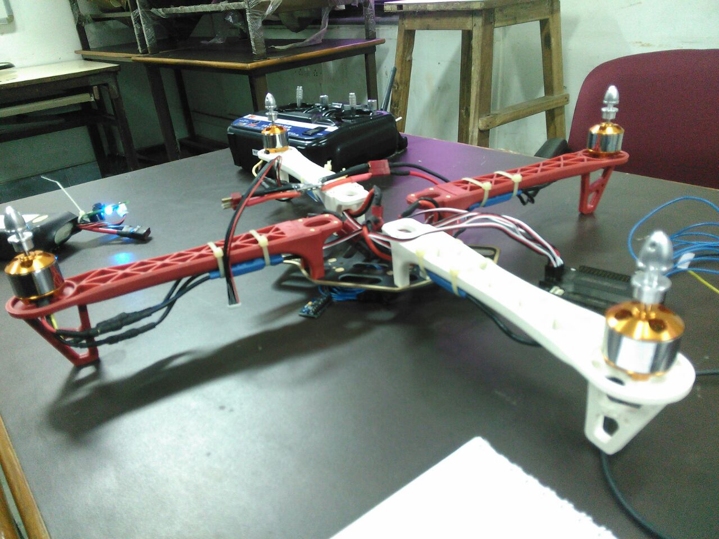
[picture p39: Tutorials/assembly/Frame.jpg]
		
		\caption{Frame Assembly w/o upper plate mounted.}
		\end{figure}
		
		\subsection{Mounting your Flight Controller}
		For the autonomous drone application we are usin APM 2.6 as our flight controller, but you can use any flight controller of your choice like KK 2.x board, CC3D, Naze 32, Pixhawk, KISS,etc. The basic step to mount any flight controller on the deck of the frame is by mounting it by using an anti-vibration mount. Using it is very important as it reduces the amount of vibrations that reach the controller. As unwanted vibrations can lead to erroneous results.
		\paragraph{}So were are using the antivibration mount for the APM. So depending on your flight controller you can mount it on the mount by using double sided tapes. But before mounting the vibration mount on the deck ensure that the forward direction of the FC matches with the forward direction of your quad decided by you.
		
		\subsection{Wiring the flight controller}
		Now depending on your flight controller you have to wire up your Flight controller with the receiver and the ESC's. Here we will demonstrate the connections for the APM 2.6 .
		\paragraph{} Another important note is to make the motor connections properly i.e. the first motor connects to port 1 on the APM and son on. The below pictures will make it very clear.
		\begin{figure}[h]
	 	\centering
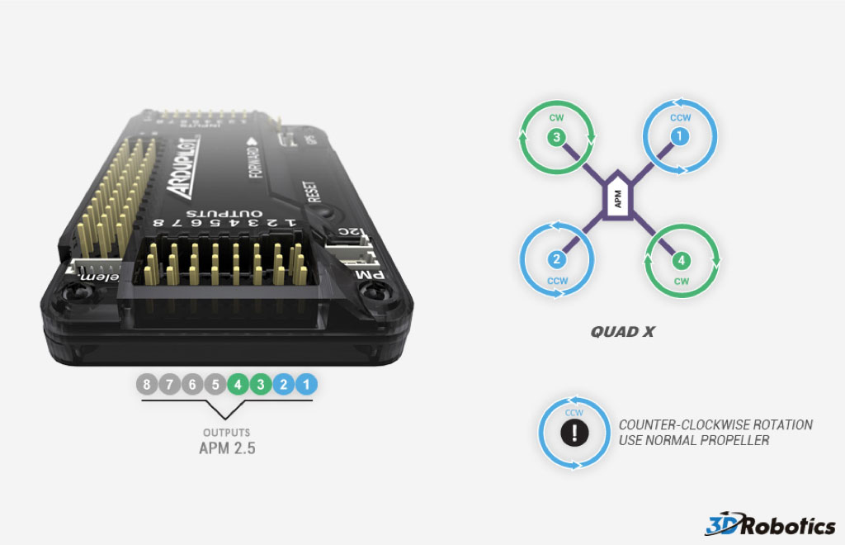
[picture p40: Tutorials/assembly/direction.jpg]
		
		\caption{Motor Layout For quad X config.}
		\end{figure}
		\paragraph{}Don't worry about the motor spin direction we will solve it in a moment. Now let's see how to make connections with the APM. Refer the below figure. Don't bother about the GPS and Gimbal, they are just extra accessories.
		\begin{figure}[H]
    \begin{center}
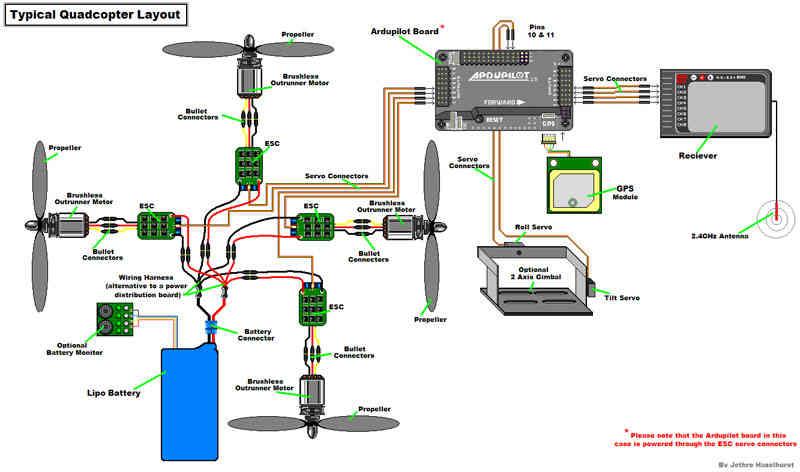
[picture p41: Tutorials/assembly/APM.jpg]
    
    \caption{APM wiring}
    \label{fig: figure}
    \end{center}
\end{figure}
	\paragraph{•}
	Now if you have followed the above steps properly, you are ready for the calibration of your flight controller. Now here we are done with the assembly.
	\section{References}
	Images are downloaded from:
	\paragraph{•}
	\url{http://ardupilot.org/copter/docs/connecting-the-apm2.html}
	\paragraph{•}\url{https://multicopterbuild.wordpress.com/how-tos/quadcopter/}
	\paragraph{•}\url{http://dronesforsaleclassified.com/product/dji-hot-wheels-diy-same-paragraph-quadcopter-frame-quality-nylon-f450-v2-rack-integrated-pcb-board-diy-drone-quadrocopter/}
	\paragraph{•}\url{http://www.flyingtech.co.uk/frames-props-parts-accessories/tarot-firefly-450-quadcopter-frame}
	
\end{document}

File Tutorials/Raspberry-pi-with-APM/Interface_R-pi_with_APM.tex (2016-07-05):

 %%%%%%%%%%%%%%%%%%%%%%%%%%%%%%%%%%%%%%%%%%%%%%%%%%%%%%%%%%%%%%%%%%%%%%%%%%%%%
%	e-Yantra, IIT-Bombay

%	Document Author: Akshit Gandhi
%	Date: 17-June,2016
%	Last Editted by: Akshit
%   Date Last updated: 17-06-2016 

%%%%%%%%%%%%%%%%%%%%%%%%%%%%%%%%%%%%%%%%%%%%%%%%%%%%%%%%%%%%%%%%%%%%%%%%%%%%%

\documentclass[11pt,a4paper]{article}
\usepackage{float}
\usepackage{graphicx}
\usepackage{hyperref}
\usepackage{float}
\title{Interfacing Raspberry-pi with APM flight controller}
\author{Akshit Gandhi \\ Keyur Rakholiya}

\date{\today}

\begin{document}
	\maketitle
	\newpage
	\tableofcontents
	\newpage
	\section{Objective}
	Topic: Interfacing Raspberry-pi with APM(ARDUPILOT) flight controller
			APM is a flight controller which performs the stabilization of quadcopter by varying the signal to the motors based upon Radio control input. It has different flight modes which we can set from remote. It also supports different sensors like GPS ,Sonar etc.
		In this tutorial we will learn to how to setup a communication between the 
		 and APM flight controller, so that we can run/write our python scripts on R-PI and execute them on our drone. We will be going into details of each step.
	\section{Prerequisites}
	 It's better if you first go through the official documentation on ardupilot's website on connecting R-PI		 with APM.\textbf{[1]}, it will be beneficial also for this tutorial and also for later tutorials.
	\section{Hardware Requirement}
	 Drone or Quadcopter, Raspberry pi, telemetry port connector for connecting APM to RPI and few jumpers(M-F).
	\section{Procedure}
	This tutorial explains how to connect and configure a Raspberry Pi (RPi) so that it is able to communicate with a APM flight controller using the MAVLink protocol\textbf{[2]} over a serial connection
	 \begin{figure}[H]
	 	\centering
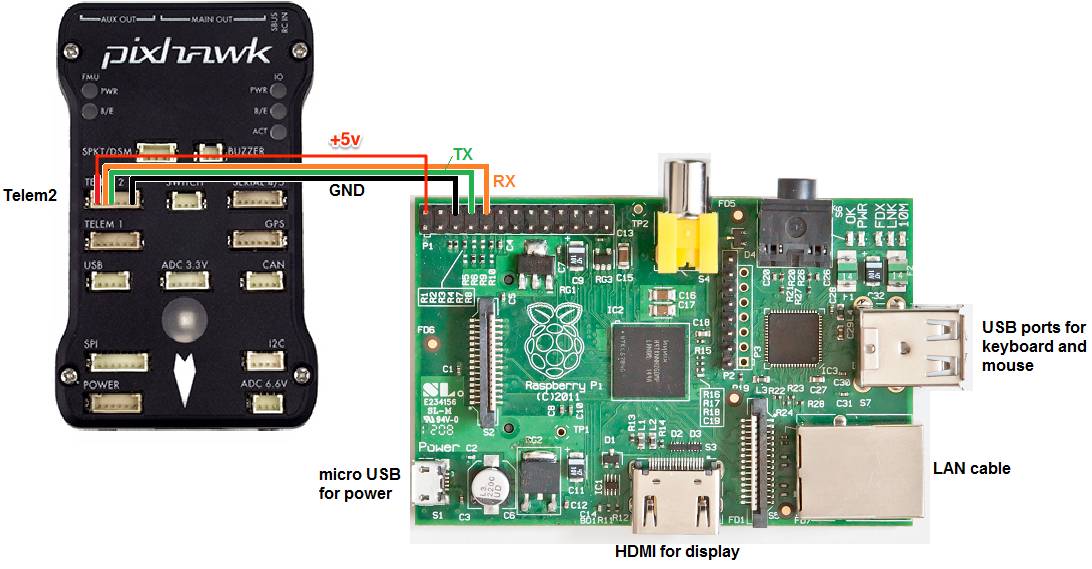
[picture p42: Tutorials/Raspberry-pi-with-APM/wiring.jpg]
		
	 	\caption{Connection diagram.}
\end{figure}
	\paragraph{•} The picture shown above is for pixhawk controller but the same connection works for APM also.
	 \subsection{Connecting to RPi with an SSH/Telnet client}
	 \textbf{NOTE:} These steps assume that you have already set-up your RPi so that it is running Raspbian.

To avoid the requirement to plug a keyboard, mouse and HDMI screen into your RPi it is convenient to be able to connect from your Desktop/Laptop computer to your RPi using an SSH/Telnet client such as PuTTY.
	 \begin{itemize}
	 	\item Connect the RPi to your local network by one of the following methods:
			\begin{itemize}
				\item Connecting an Ethernet LAN cable from the RPi board to your Ethernet router, or
				\item Use a USB dongle to connect your RPi to the local wireless network, or
				\item Connect the Ethernet LAN cable between the RPi and your desktop/laptop computer. Open the control panel’s Network and Sharing Center, click on the network connection through which your desktop/laptop is connected to the internet, select properties and then in the sharing tab, select “Allow other networks to connect through this computer’s Internet connection”
\end{itemize}
	\item Determine the RPi’s IP address:
	\begin{itemize}
		\item If you have access to the RPi’s terminal screen (i.e.you have a screen, keyboard, mouse connected) you can use the /sbin/ifconfig command.
			\begin{figure}[H]
				\centering
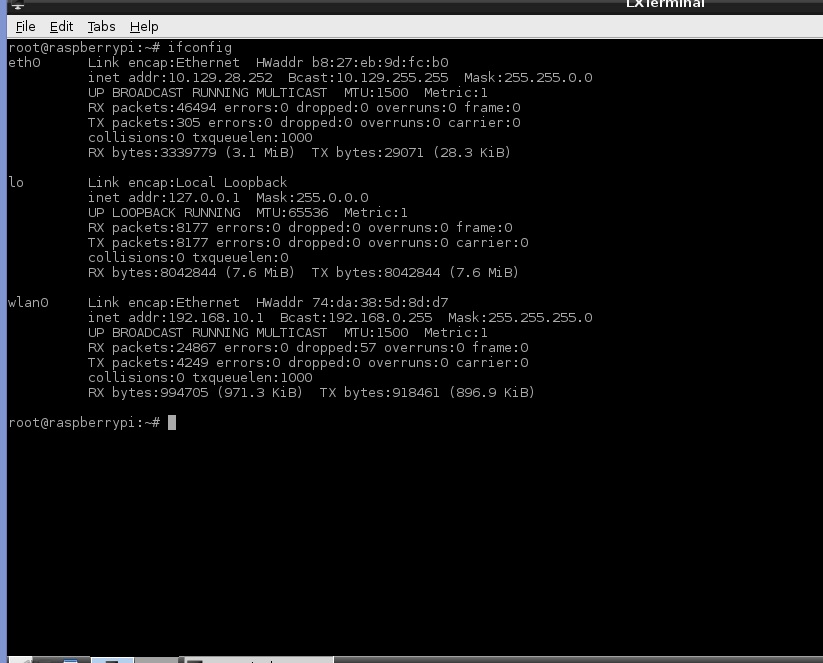
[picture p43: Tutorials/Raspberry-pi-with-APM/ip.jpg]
				
				\caption{ip address on terminal.}
			\end{figure}
		\item If your Ethernet router has a web interface it may show you the IP address of all connected devices
	\end{itemize}	\item Connect with Putty:
		\begin{figure}[H]
	 	\centering
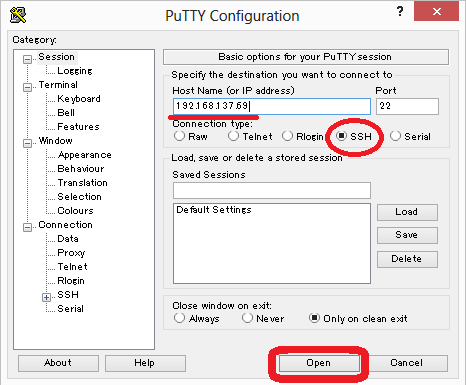
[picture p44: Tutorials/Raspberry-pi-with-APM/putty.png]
		
	 	\caption{Connect screen with Putty.}
\end{figure}
	If all goes well you should be presented with the regular login prompt to which you can enter the username/password which defaults to pi/raspberry
	 \end{itemize}
	 \subsection{Install the required packages on the Raspberry Pi}
	 Log into the RPi board (default username password is pi/raspberry) and check that its connection to the internet is working. If there's some problem then troubleshooting guide can be found on the documentation site \url{http://ardupilot.org/dev/docs/raspberry-pi-via-mavlink.html}
	 \paragraph{After the internet connection is confirmed to be working install these packages:}
	 \begin{itemize}
	 	\item sudo apt-get update
	 	\item sudo apt-get install screen python-wxgtk2.8 python-matplotlib python-opencv python-pip python-numpy python-dev libxml2-dev libxslt-dev
	 	\item sudo pip install pymavlink
	 	\item sudo pip install mavproxy
	 \end{itemize}
	 \subsection{Disable the OS control of the serial port}
	 Use the Raspberry Pi configuration utility for this.
		\paragraph{}Type:
			\begin{itemize}
				\item sudo raspi-config
				\item And in the utility, select 								“Advanced Options”:
				\begin{figure}[H]
	 	\centering
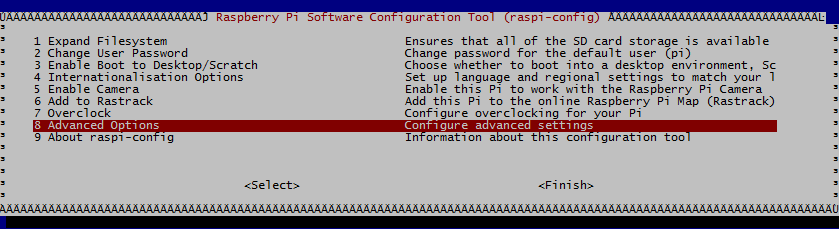
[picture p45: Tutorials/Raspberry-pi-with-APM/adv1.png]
		
	 	\caption{RasPiConfiguration Utility: Serial Settings: Advanced Options.}
\end{figure}
		\begin{itemize}
			\item And then “Serial” to disable OS use of the serial connection:
			\begin{figure}[H]
	 	\centering
		
\end{figure}
		\end{itemize}
Reboot the Raspberry Pi when you are done.
			\end{itemize}
			\subsection{Testing the connection}
			To test the RPi and APM are able to communicate with each other first ensure the RPi and APM are powered, then in a console on the RPi type:
			\begin{itemize}
				\item sudo -s
				\item mavproxy.py --master=/dev/ttyAMA0 --baudrate 57600 --aircraft MyCopter
				
				raspberry pi's default port is connected with console input/output. so use this port we have to disable it first. now we have connected our device via UART port ot R-Pi. so "/dev/ttyAMA0" is a port for serial communication between R-pi and APM. 
				
				You configure BaudRate as bits per second. The transferred bits include the start bit, the data bits, the parity bit (if used), and the stop bits. However, only the data bits are stored.
				
				The baud rate is the rate at which information is transferred in a communication channel. In the serial port context, "9600 baud" means that the serial port is capable of transferring a maximum of 9600 bits per second. If the information unit is one baud (one bit), the bit rate and the baud rate are identical. If one baud is given as 10 bits, (for example, eight data bits plus two framing bits), the bit rate is still 9600 but the baud rate is 9600/10, or 960. You always configure BaudRate as bits per second. Therefore, in the previous example, set BaudRate to 9600.

				Note: In the above command it's MyCopter and My-Copter
				\item Once MAVProxy has started you should be able to type in the following command to display the \texttt{ARMING\_CHECK} parameters value
				\begin{itemize}
					\item param show \texttt{ARMING\_CHECK}
					\item param set \texttt{ARMING\_CHECK} 0
					\item arm throttle
					\begin{itemize}
			\item And then “Serial” to disable OS use of the serial connection:
			\begin{figure}[H]
	 	\centering
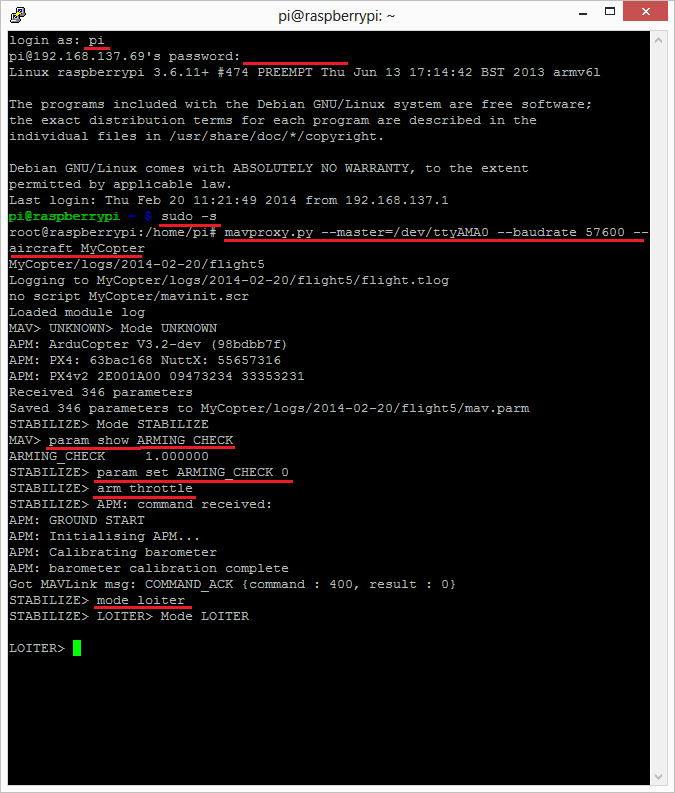
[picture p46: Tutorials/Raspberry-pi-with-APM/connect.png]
		
		\caption{Terminal screen.}
\end{figure}
	\textbf{NOTE:} If you get an error about not being able to find log files or if this example otherwise doesn’t run properly, make sure that you haven’t accidentally assigned these files to another username, such as Root.
	\paragraph{•}Entering the following at the Linux command line will ensure that all files belong to the standard Pi login account:
	\item sudo chown -R pi /home/pi
		\end{itemize}
				\end{itemize}
				
			\end{itemize}
			\subsection{Configure MAVProxy to always run}
				To setup MAVProxy to start whenever the RPi is restarted open a terminal window and edit the /etc/rc.local file, adding the following lines just before the final “exit 0” line: 
				\begin{figure}[H]
	 	\centering
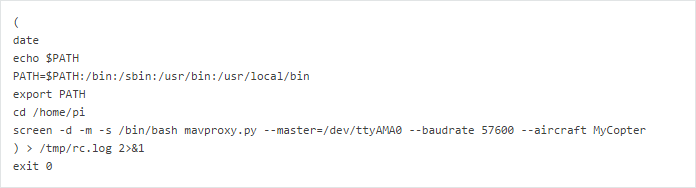
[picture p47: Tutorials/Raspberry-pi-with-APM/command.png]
		
		
\end{figure}
\paragraph{To open /etc/rc.local file type in sudo nano /etc/rc.local and type the code below and save it in the file}
\paragraph{}If you wish to connect to the MAVProxy application that has been automatically started you can log into the RPi and type: sudo screen -x
\paragraph{•}It is also worth noting that MAVProxy can do a lot more than just provide access to your APM. By writing python extension modules for MAVProxy you can add sophisticated autonomous behaviour to your vehicle. A MAVProxy module has access to all of the sensor information that your APM has, and can control all aspects of the flight.
	\section{References}
	\paragraph{•}
	\textbf{[1]}\url{http://ardupilot.org/dev/docs/raspberry-pi-via-mavlink.html}
	\textbf{[2]}\url{http://qgroundcontrol.org/mavlink/start}
	\url{http://ardupilot.org/dev/docs/raspberry-pi-via-mavlink.html}
		
	\paragraph{Everything mentioned above bit by bit is from the official documentation.}
	
\end{document}

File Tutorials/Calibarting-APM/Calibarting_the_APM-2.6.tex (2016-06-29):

 %%%%%%%%%%%%%%%%%%%%%%%%%%%%%%%%%%%%%%%%%%%%%%%%%%%%%%%%%%%%%%%%%%%%%%%%%%%%%
%	e-Yantra, IIT-Bombay

%	Document Author: Akshit Gandhi
%	Date: 7-June,2016
%	Last Editted by: Akshit
%   Date Last updated: 16-06-2016 

%%%%%%%%%%%%%%%%%%%%%%%%%%%%%%%%%%%%%%%%%%%%%%%%%%%%%%%%%%%%%%%%%%%%%%%%%%%%%

\documentclass[11pt,a4paper]{article}
\usepackage{float}
\usepackage{graphicx}
\usepackage{hyperref}
\usepackage{float}
\title{Calibrating the APM}
\author{Akshit Gandhi \\ Keyur Rakholiya}
\date{\today}

\begin{document}
	\maketitle
	\newpage
	\tableofcontents
	\newpage
	\section{Objective}
	Topic: Calibrating the APM 2.6/2.5
		In this tutorial we will learn to how to calibrate our APM flight controller. We will be going into details of each step.
	\section{Prerequisites}
	 It's better if you first go through the official documentation on ardupilot's website. The link is: \url{http://ardupilot.org/copter/index.html}, it will be beneficial also for this tutorial and also for later tutorials. Install Mission Planner Software link is: \url{http://firmware.ardupilot.org}
	\section{Hardware Requirement}
	 Drone or Quadcopter, USB cable, a Computer.
	\section{Calibration Process}
	 So, now we start with the process of calibrating the APM. \textbf{Note:} There is are lot's of improvement going on with the APM firmwares and with the associated softwares, so it is advised that you use a more latest software and firmware as it is a refinement of the previous version, but at the time we were working on this project we found that the latest firmware for APM-2.6 was ACv3.3.3 but no-where we could find this firmware so we switched to a previous firmware which was ACv3.2.1 and also to ACv3.1.5.
	 \paragraph{•}Mission Planner is a ground control station for Plane, Copter and Rover. It is compatible with Windows only. Mission Planner can be used as a configuration utility or as a dynamic control supplement for your autonomous vehicle.
	 \paragraph{•}We found out that the latest version of Mission Planner should support for the latest version of the APM firmware, so we had to switch to a more previous version of the Mission Planner software. Mission Planner is software which will help us throughout the calibration process and many more times as we will see later. The Mission Planner Software we are using is V1.3.30 which should look something like this: 
	 \begin{figure}[H]
	 	\centering
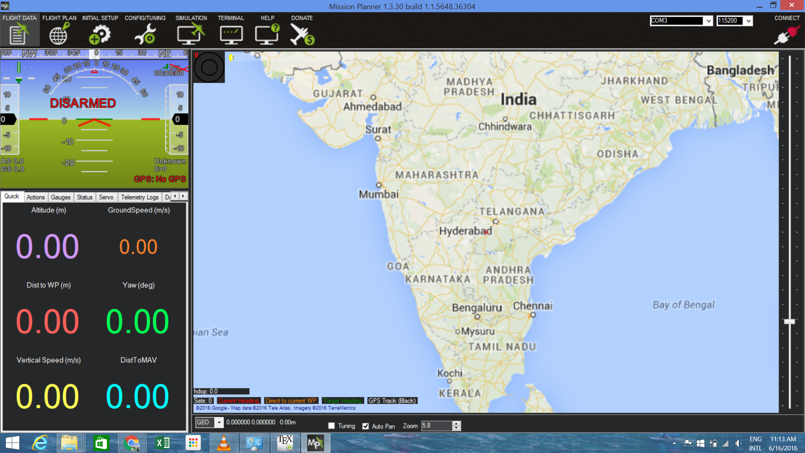
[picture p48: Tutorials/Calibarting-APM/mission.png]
		
	 	\caption{Mission Planner.}
\end{figure}
	 \subsection{Installing Mission Planner}
	 The very first step is to install the mission planner software. It is known as GCS or Ground control system. It can be downloaded form here: \url{http://firmware.ardupilot.org/Tools/MissionPlanner/MissionPlanner-latest.msi} \textbf{Note} This link will automatically download the latest version, so if you want to download the previous versions than you can go to \url{http://firmware.ardupilot.org}
	 \paragraph{•}After downloading the software go through the installation process. Follow the instructions to complete the setup process. The installation utility will automatically install any necessary software drivers. If you receive a DirectX installation error, please update your DirectX plug-in from the DirectX Download Center link is: \url{http://www.microsoft.com/en-us/download/details.aspx?id=35}.
	 \paragraph{}If you receive the warning pictured in Fig 2, select Install this driver software anyway to continue.
	 \begin{figure}[H]
	 	\centering
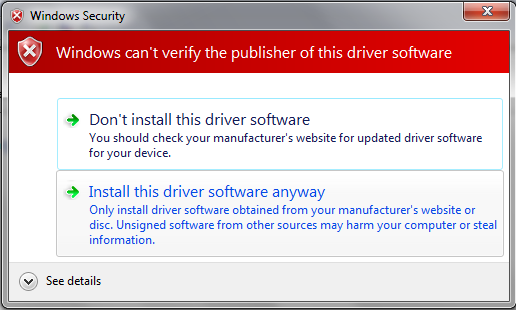
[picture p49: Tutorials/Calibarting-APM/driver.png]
		
	 	\caption{Warning Screen.}
\end{figure}

An icon to open the Mission Planner is created according to your instructions during the installation.

	\subsection{Loading Firmware into APM 2.6}
		\subsubsection{Connection}Connect controller to computer
Once you’ve installed the Mission Planner onto your computer, connect the autopilot board to your computer using the micro USB cable as shown below. Use a direct USB port on your computer (not a USB hub).
		\begin{figure}[H]
	 	\centering
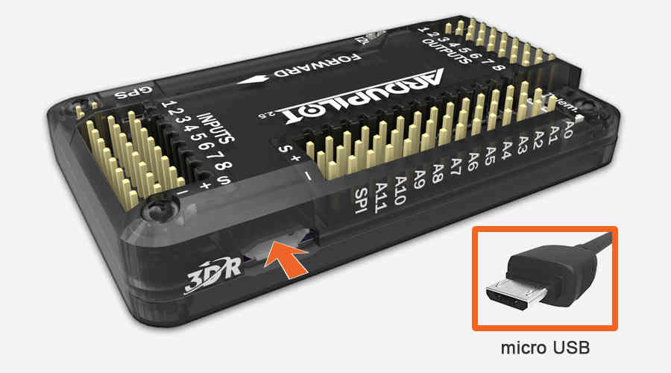
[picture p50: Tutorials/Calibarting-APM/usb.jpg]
		
	 	\caption{APM USB Connection.}
		\end{figure}
		
		\subsubsection{Connect to Mission Planner}
Open the Mission Planner and select the COM port drop-down on the upper-right corner of the screen (near the Connect button). Select AUTO or the specific port for your board (Arduino Mega 2560). Set the Baud rate to 115200 as shown. Don’t hit Connect just yet.
\begin{figure}[H]
	 	\centering
		
	 	\caption{COM Port.}
		\end{figure}	
		
		\subsubsection{Install firmware}
On the Mission Planner’s Initial Setup | Install Firmware screen select the appropriate icon that matches your frame (i.e. Quad, Hexa). Answer Yes when it asks you “Are you sure?”.
		\begin{figure}[H]
	 	\centering
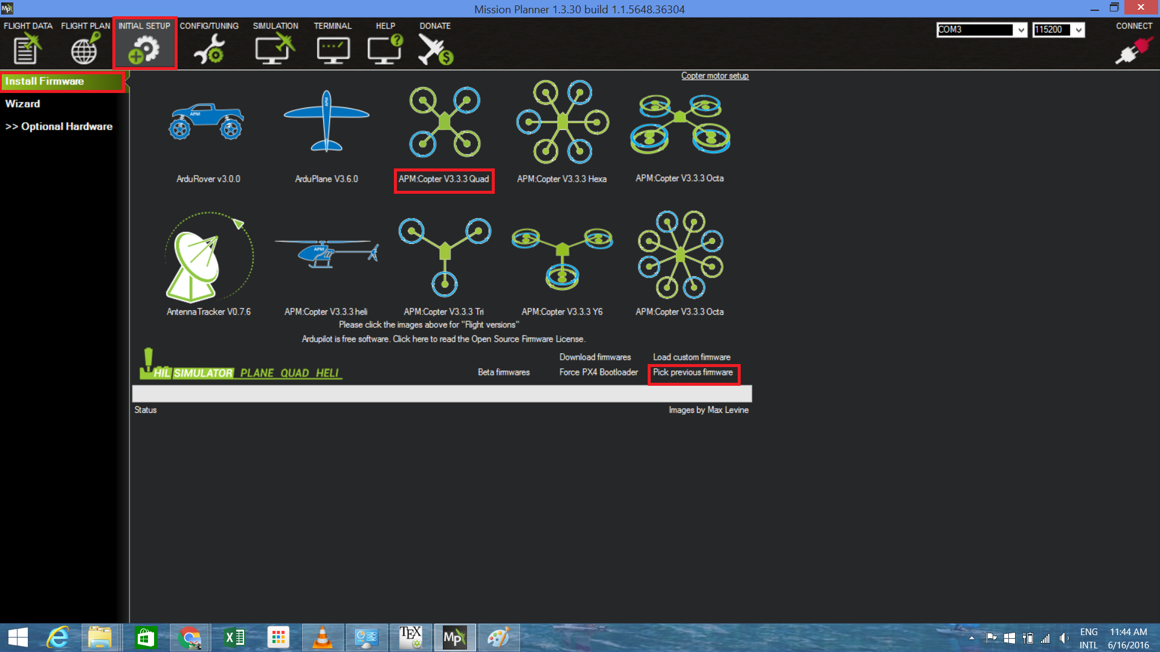
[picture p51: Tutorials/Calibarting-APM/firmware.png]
		
	 	\caption{Install Firmware Screen.}
		\end{figure}
		\paragraph{•}Here you will see that the version shown is AC3.3.3 but if you want to use a previous version than you can select pick previous firmware and from the dropdown you can select the required version in this case v3.2.1. If all goes well you will see some status appear on the bottom right including the words, “erase...”, “program...”, “verify..” and “Upload Done”. The firmware has been succesfully uploaded to the board.
		
		\subsection{Calibrating the APM}
			Once you have installed the firmware and if the APM is not connected to the mission planner then click on the connect button on the top right corner. Once the board is connected \paragraph{•} Click on Mandatory Hardware and you will see a dropdown with options like Frame Type, Acc Calibration, etc. Follow the steps in each option and go through the instructions and it should successfully calibrate the APM.
			\paragraph{•} If you need any assistance on how to calibrate then you can check out this link: \url{http://ardupilot.org/copter/docs/configuring-hardware.html} and go through the step by step guide on whole calibration process
		
		\subsection{Testing}
		You can test the firmware is basically working by switching to the Mission Planner Flight Data screen and pressing the Connect button. The HUD should update as you tilt the board.
		
		\subsection{Troubleshooting}
		If Mission planner is unable to connect:

\paragraph{}1. Check that the correct baud rate is used for the selected method (115200 on USB or 57600 on Radio/Telemetry)
\paragraph{}2. If using a COM port on Windows, check that the connection’s COM port exists in the Windows Device Manager’s list of serial ports.
\paragraph{}3. If using a USB port, try a different physical USB port
	\paragraph{}You should also ensure that the autopilot controller board has appropriate ArduPilot firwmare installed and has booted correctly (on APM there are useful LEDs which can tell you the state of the autopilot).
	
	\paragraph{So, if you follow this tutorial properly you should be able to calibrate the APM successfully. You may face some errors like INS not calibrated, Compass/Gyro bad health, RC not calibrated, we suggest that you should go through the process once again and if the error persists then you can find about it's troubleshooting on the net!}
	\section{References}
	\paragraph{•}
	\url{http://ardupilot.org/planner/docs/common-install-mission-planner.html}
	\paragraph{•}\url{http://ardupilot.org/planner/docs/common-loading-firmware-onto-pixhawk.html}
	\paragraph{•}\url{http://ardupilot.org/planner/docs/common-connect-mission-planner-autopilot.html}
	\paragraph{}Everything mentioned above has been referred from the official documentation.
	
\end{document}

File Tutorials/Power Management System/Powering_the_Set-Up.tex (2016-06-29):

 %%%%%%%%%%%%%%%%%%%%%%%%%%%%%%%%%%%%%%%%%%%%%%%%%%%%%%%%%%%%%%%%%%%%%%%%%%%%%
%	e-Yantra, IIT-Bombay

%	Document Author: Akshit Gandhi
%	Date: 20-June,2016
%	Last Editted by: Akshit
%   Date Last updated: 20-06-2016 

%%%%%%%%%%%%%%%%%%%%%%%%%%%%%%%%%%%%%%%%%%%%%%%%%%%%%%%%%%%%%%%%%%%%%%%%%%%%%

\documentclass[11pt,a4paper]{article}
\usepackage{float}
\usepackage{graphicx}
\usepackage{hyperref}
\title{Power Management System for the Autonomous-Drone.}
\author{Akshit Gandhi \\ Keyur Rakholiya}
\date{\today}

\begin{document}
	\maketitle
	\newpage
	\tableofcontents
	\newpage
	\section{Objective}
	Topic: Power Management System for the Autonomous-Drone.
		This tutorial is a demonstration about how we made a power management system for the Autonomous-Drone setup which uses Raspberry-Pi, APM-2.6 flight controller and other mandatory electronics.
	\section{Hardware Requirement}
	 Few Jumper Cables, that's it!
	\section{Assembly}
	 So, now as we want to now, mount the R-Pi on the F450 frame and power it using the Lipo 3s battery. The battery which we are using is LiPo 3s (11.1V), 5000 mAh and 20C battery. The problem here is that R-Pi works on 5V and 1.8Amps, so at the beginning we decided to make a circuit that will be used to power up the R-Pi from 11.1V battery, but there would be some power consumption from the circuit itself.\paragraph{•} So we found that we could also power the R-Pi from the UART cable (as we are connecting APM and R-Pi using UART) but the current requirements were not satisfied as were using a Wifi adapter to remotely login into R-Pi. Then came the idea to power the R-Pi using the BEC (Battery Eliminator Circuit) which is present in the ESC and the specifications too matched the R-Pi input specs, the esc's provided 5V and 2A output voltage. So we decided to connect the the 5V pin on R-Pi (of our UART connection) to the +ve rail on the ESC connection side on APM.
	 \subsection{Mounting the R-Pi}
	 	Firstly to mount the R-Pi we prepared a 3D printed base with holes to mount the R-Pi on that base, because we wanted to ensure that no part of R-Pi PCB to get shorted with the Power Distribution Board on the F450 frame. Then we sticked the base onto the frame using double sided tape and cable ties. So, it looked something like this:
	 	\begin{figure}[H]
	 	
	 	\centering
		
	 	\caption{R-Pi Mounted on the Frame.}
\end{figure}
	 	\subsection{Powering the Rpi from APM}
	 	The below figure shows how to power the Rpi from the APM board by connecting a pin on positive rail on the ESC side to the UART +ve pin, and ensure that the ground pin of UART on Rpi is connected to ground of UART on Telemetry port of APM and not at Ground pin of ESC.
	 	\begin{figure}[H]
	 	\centering
		
	 	\caption{R-Pi Mounted on the Frame.}
\end{figure}
\end{document}

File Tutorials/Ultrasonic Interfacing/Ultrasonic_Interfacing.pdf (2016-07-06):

## Interface Ultrasonic Sensor with R-Pi

Akshit Gandhi
Keyur Rakholiya

July 6, 2016

1

## Contents

1 Tutorial Name | 3
2 Prerequisites | 3
3 Hardware Requirement | 3
4 Theory and Description | 3
5 References | 5

2

## 1 Tutorial Name

Interfacing Ultrasonic sensor with Raspberry Pi.

Objective

In this tutorial we will be going through on how to interface an ultrasonic sensor with R-Pi. The Ultrasonic Sensor which we will be using is the HC-SR04. The HC-SR04 sensor cannot be directly used with the R-Pi, we need a voltage divider circuit, the reason will be explained in the later sections.

The reason for using ultrasonic sensor with the quadcopter setup is that, when flying indoors autonomously we need some sort of sensor that will provide the altitude details of the quadcopter, we know that the APM 2.6 has the Barometer Sensor, but the limitation is that it is accurate only above 5 meters height (altitude). So, we need an Ultrasonic Sensor for height (altitude) measurement.

We also tried interfacing the Sonar Sensor which is compatible with the APM 2.6. The Sonar we used is the [Maxbotic Sonar MB-1200 series]. But it didn’t give us the desired results. So, we moved onto using the HC-SR04.

## 2 Prerequisites

Knowledge of voltage divider circuit.

## 3 Hardware Requirement

R-Pi, wires, HC-SR04 sensor, 1000 Ohm and 680 Ohm resistances (1 each)

## 4 Theory and Description

### 4.1 Connecting to R-Pi

Powering the module is easy. Just connect the +5V and Ground pins to Pin 2 and GPIO21 on the Pis GPIO header.

The input pin on the module is called the trigger as it is used to trigger the sending of the ultrasonic pulse. Ideally it wants a 5V signal but it works just fine with a 3.3V signal from the GPIO. So we connected the trigger directly to GPIO20 on our GPIO header.

3

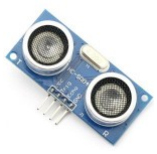
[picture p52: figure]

Figure 1: HC-SR04 Sensor

You can use any GPIO pins you like on your RPi but you will need to note the references and amend your Python script accordingly.

The modules output is called the echo and needs a bit more thought. The output pin is low (0V) until the module has taken its distance measurement. It then sets this pin high (+5V) for the same amount of time that it took the pulse to return. So our script needs to measure the time this pin stays high. The module uses a +5V level for a high but this is too high for the inputs on the GPIO header which only like 3.3V. In order to ensure the Pi only gets hit with 3.3V we can use a basic voltage divider. This is formed with two resistors.

If R1 and R2 are the same then the voltage is split in half. This would give us 2.5V. If R2 is twice the value of R1 then we get 3.33V which is fine. So ideally you want R2 to be between R1 and R1 x 2. But we used 1000 and 680 ohm resistors (Because it worked the best for us!).

Here is a diagram of our final circuit. We chose GPIO20 and GPIO16 [echo], but you can use any of the available GPIO pins on the GPIO header. Just remember to update the script.

4

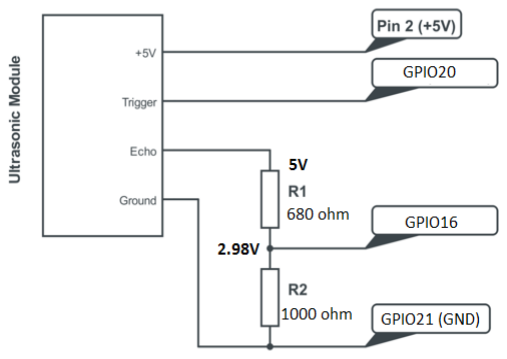
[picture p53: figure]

Figure 2: Circuit Diagram

### 4.2 Python Script

Once you have followed above connection diagram you can test the sensor you are ready with the next part i.e to access the sensor values using the python script. The script is in the codes folder.

### 4.3 Accuracy

- The accuracy of the distance measurement is dependent on timing. Python under Linux is not ideal for precise timing but for general messing about it will work OK. To improve accuracy you would need to start looking at using C instead.
- When the GPIOs are configured the module needs some time before it is ready to take its first reading so we added a 0.5 second delay to the start of the script.
- The transducers have a wide angle of sensitivity. In a cluttered environment you may get shorter readings due to objects to the side of the module.
- Measurements work down to about 2cm. Below this limit the results can give strange results.
- If the ultrasonic transducers touch anything the results are unpredictable.

## 5 References

For more understanding you can visit the below two sites: http://www.raspberrypi-spy.co.uk/2012/12/ultrasonic-distance-measurement-using-python-part-1/http://www.modmypi.com/blog/hc-sr04-ultrasonic-range-sensor-on-the-raspb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

5

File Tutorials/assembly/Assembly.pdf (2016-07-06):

## Assembling The Quadcopter

Keyur Rakholiya
Akshit Gandhi

July 5, 2016

1

## Contents

2

## 1 Objective

Topic: Assembling the quadcopter In this tutorial we will study about the assembling of the quadcopter.

## 2 Prerequisites

refer the previous tutorial first. 1. calculation
choose your flight controller, motors,propellers,frame,battery.

## 3 Hardware Requirement

All the components mentioned previously and a Soldering kit, deans connector and wires, M3*8 screws.

## 4 Assembly

So, now we start with the assembly of the quad, ensure you have all the components mentioned previously.

### 4.1 Assembling the Motors

Once you get the motors, the very first job is to mount the motors on the F450 frame. For this you will need M3 screws, so with the help of a screwdriver or L-key mount the motors on the arm of the quad like this:

### 4.2 Esc mount

After the motors have been attached on the arms, next job is to attach the esc’s, you can tie individual esc’s on the arms using cable ties as shown below.
Also connect 3 wires from the esc’s to the 3 wires on the motor, don’t worry about the order in which the wires have to be connected we will look upon that in later tutorials.on ce your arms are ready with the escs and motors it will look something like this:

### 4.3 Connecting Esc to Power distribution board

The F450 frame comes with an inbuilt power distribution board so you just need to solder the esc wires (both positive and ground) to the pcb on the base plate. The pcb would look something like this.
You will see that there are some points to attach the esc’s marked as + or
- and also on extra pair of points will be there for connecting the battery to the distribution board. First you need to ensure that there are no connectors

3

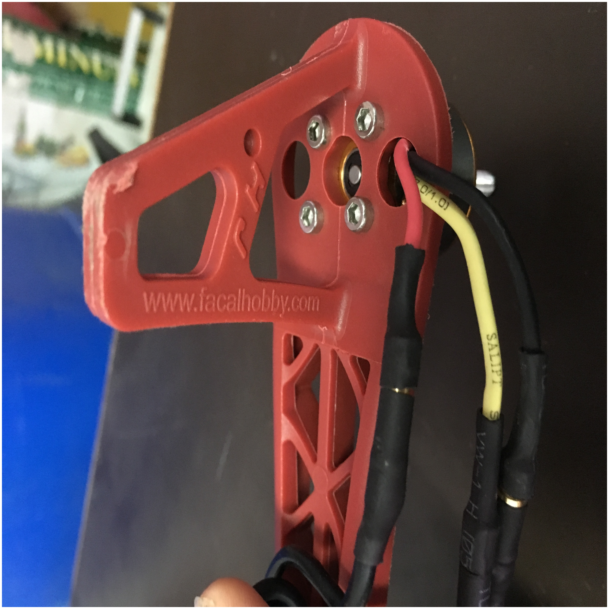
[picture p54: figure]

Figure 1: installing motors

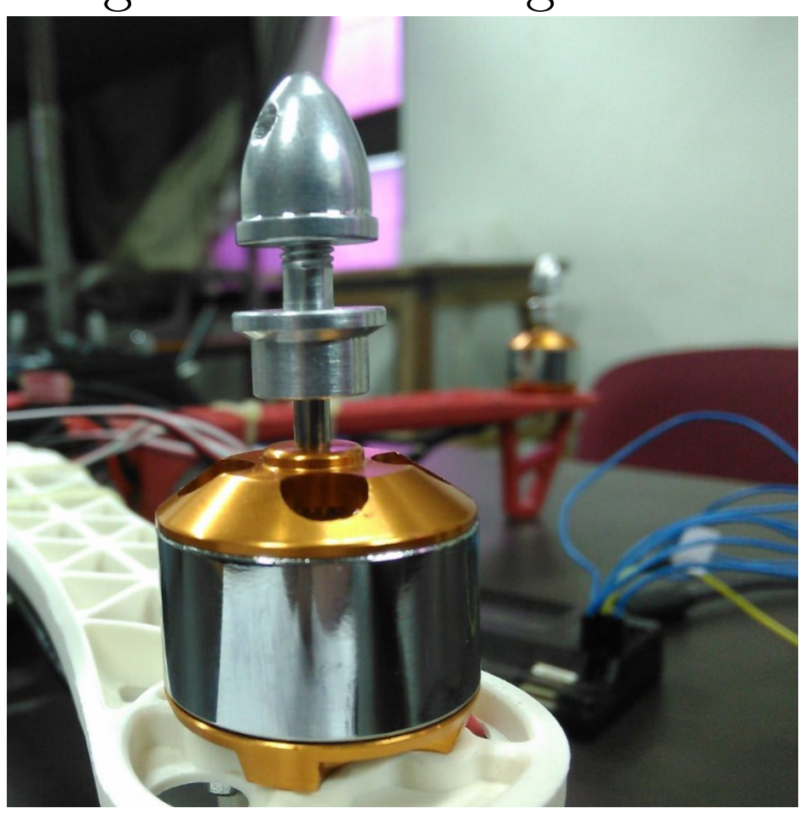
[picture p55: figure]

Figure 2: Motor Assembly.

on the esc( on the +ve and -ve wires), if there are any connectors desolder them and then solder the wires onto the pcb. Special care to ensure that +ve wires is soldered onto the +ve of the pcb and respectively for negative. Once you have soldered the wires onto the assembly would look something like this:

### 4.4 Putting the frame together

Now you have your frame ready the next step is to use the screws provided with the kit to mount the arms on the lower plate and after that attach the upper plate. After this step your quad should look like this:

But an IMPORTANT note: To make it easy for you to know the orientation of the quad you can setup the frame in such a way that 2 adjacent white/red arms point to the forward direction of the quad.

4


Figure 3: Esc Assembly.


Figure 4: Power distribution Board.

### 4.5 Mounting your Flight Controller

For the autonomous drone application we are usin APM 2.6 as our flight controller, but you can use any flight controller of your choice like KK 2.x board, CC3D, Naze 32, Pixhawk, KISS,etc. The basic step to mount any flight controller on the deck of the frame is by mounting it by using an anti-vibration mount. Using it is very important as it reduces the amount of vibrations that reach the controller. As unwanted vibrations can lead to erroneous results.

So were are using the antivibration mount for the APM. So depending on your flight controller you can mount it on the mount by using double sided tapes. But before mounting the vibration mount on the deck ensure that

5

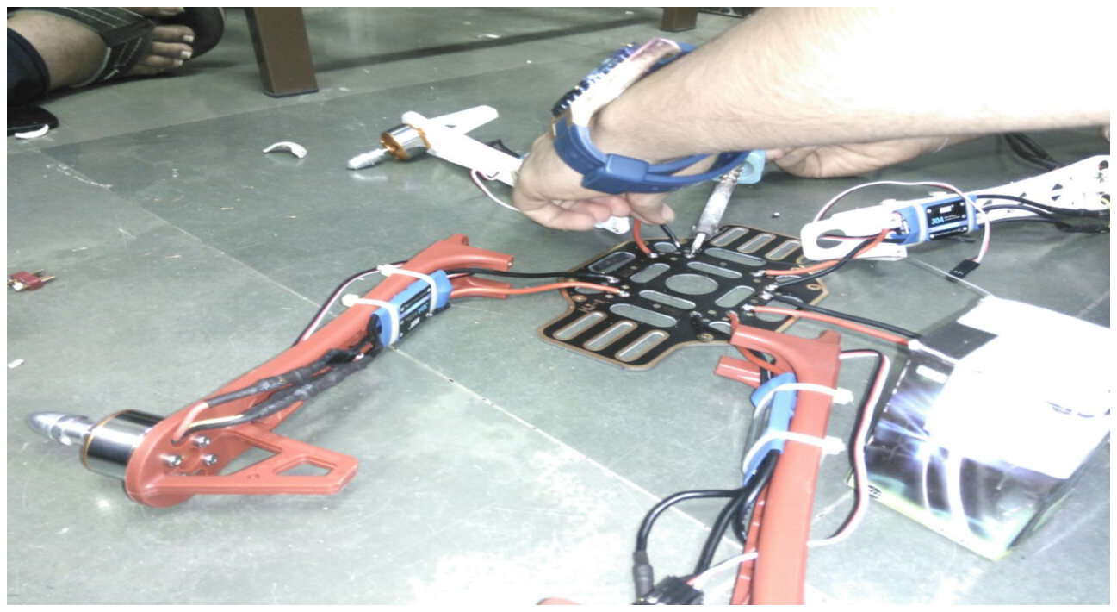
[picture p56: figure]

Figure 5: Soldering.

the forward direction of the FC matches with the forward direction of your quad decided by you.

### 4.6 Wiring the flight controller

Now depending on your flight controller you have to wire up your Flight controller with the receiver and the ESC’s. Here we will demonstrate the connections for the APM 2.6 .

Another important note is to make the motor connections properly i.e. the first motor connects to port 1 on the APM and son on. The below pictures will make it very clear.

Don’t worry about the motor spin direction we will solve it in a moment. Now let’s see how to make connections with the APM. Refer the below figure. Don’t bother about the GPS and Gimbal, they are just extra accessories.

6

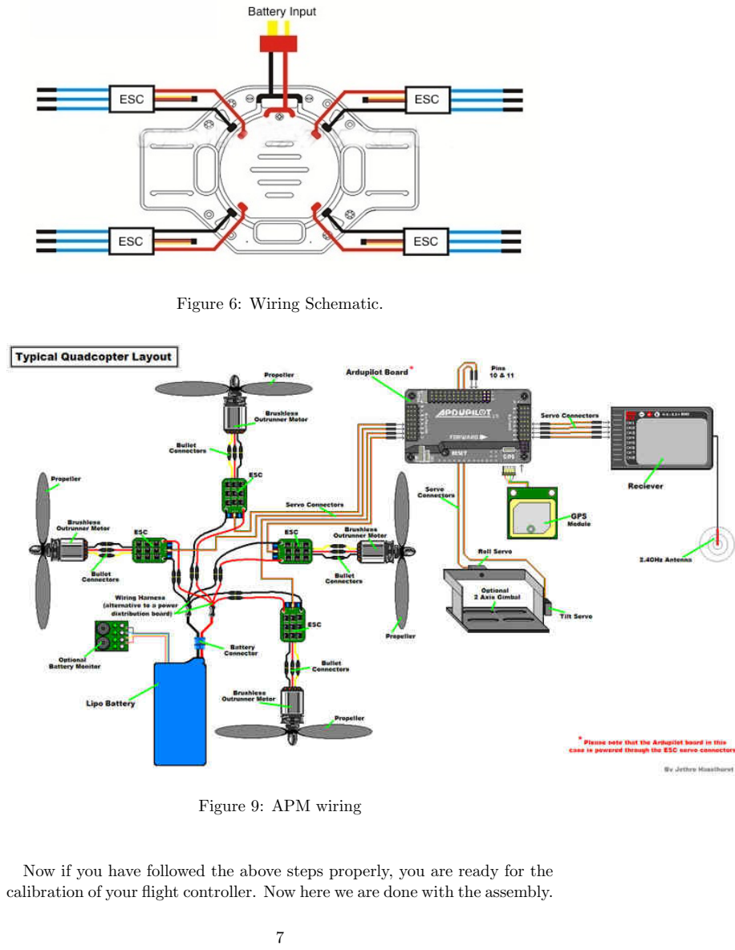
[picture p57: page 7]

Figure 6: Wiring Schematic.

Figure 9: APM wiring

Now if you have followed the above steps properly, you are ready for the calibration of your flight controller. Now here we are done with the assembly.

7

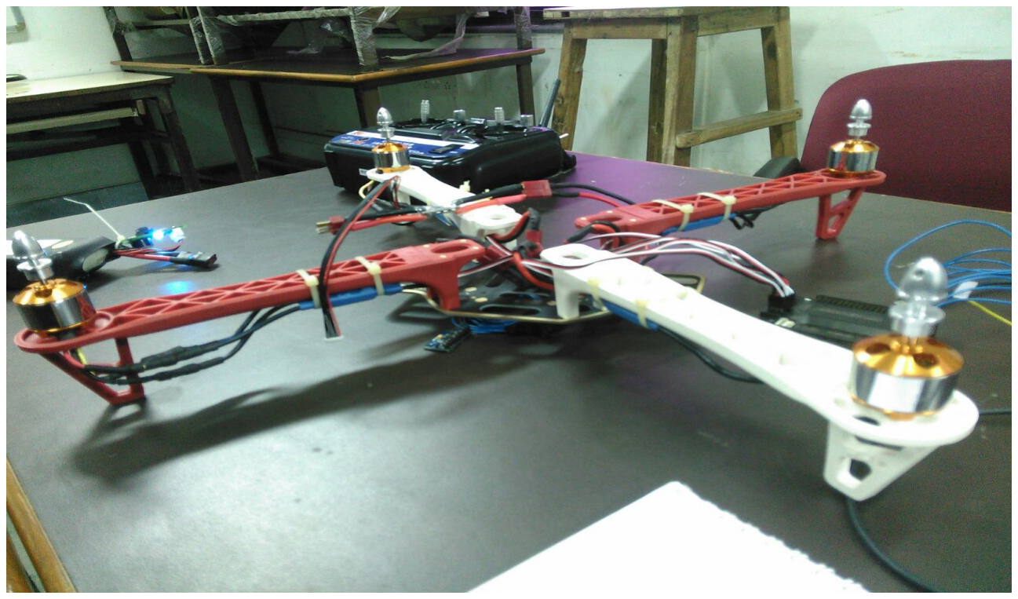
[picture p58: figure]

Figure 7: Frame Assembly w/o upper plate mounted.

## 5 References

Images are downloaded from:

http://ardupilot.org/copter/docs/connecting-the-apm2.html

https://multicopterbuild.wordpress.com/how-tos/quadcopter/

http://dronesforsaleclassified.com/product/dji-hot-wheels-diy-same-paragraph-quadcopter-frame-quality-nylon-f450-v2-rack-integrated-pcb-board-diy-drone-quadrocopter/

http://www.flyingtech.co.uk/frames-props-parts-accessories/tarot-firefly-450-quadcopter-frame

8

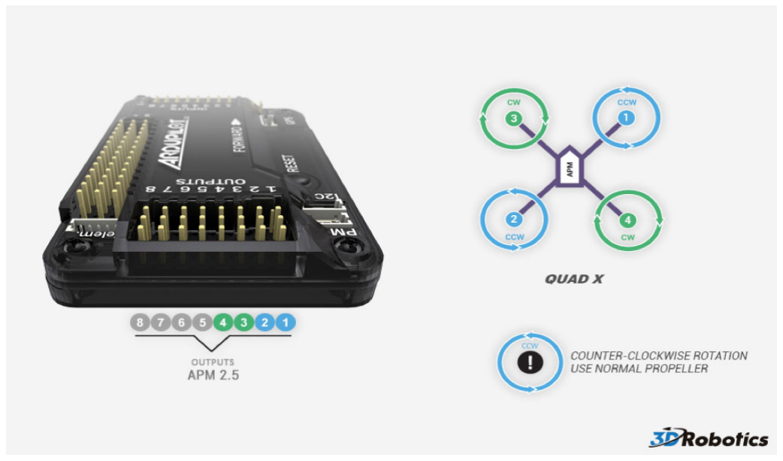
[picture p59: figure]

Figure 8: Motor Layout For quad X config.

9

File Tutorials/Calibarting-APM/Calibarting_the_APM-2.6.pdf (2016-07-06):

## Calibrating the APM

Akshit Gandhi
Keyur Rakholiya

July 5, 2016

1

## Contents

1 Objective | 3
2 Prerequisites | 3
3 Hardware Requirement | 3
4 Calibration Process | 3
5 References | 8

2

## 1 Objective

Topic: Calibrating the APM 2.6/2.5 In this tutorial we will learn to how to calibrate our APM flight controller. We will be going into details of each step.

## 2 Prerequisites

It’s better if you first go through the official documentation on ardupilot’s website. The link is: http://ardupilot.org/copter/index.html, it will be beneficial also for this tutorial and also for later tutorials. Install Mission Planner Software link is: http://firmware.ardupilot.org

## 3 Hardware Requirement

Drone or Quadcopter, USB cable, a Computer.

## 4 Calibration Process

So, now we start with the process of calibrating the APM. Note: There is are lot’s of improvement going on with the APM firmwares and with the associated softwares, so it is advised that you use a more latest software and firmware as it is a refinement of the previous version, but at the time we were working on this project we found that the latest firmware for APM-2.6 was ACv3.3.3 but no-where we could find this firmware so we switched to a previous firmware which was ACv3.2.1 and also to ACv3.1.5.

Mission Planner is a ground control station for Plane, Copter and Rover. It is compatible with Windows only. Mission Planner can be used as a configuration utility or as a dynamic control supplement for your autonomous vehicle.

We found out that the latest version of Mission Planner should support for the latest version of the APM firmware, so we had to switch to a more previous version of the Mission Planner software. Mission Planner is software which will help us throughout the calibration process and many more times as we will see later. The Mission Planner Software we are using is V1.3.30 which should look something like this:

3

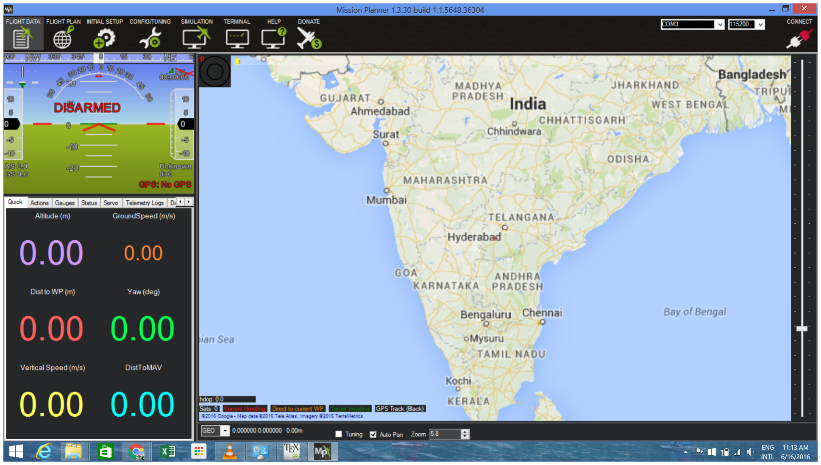
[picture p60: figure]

Figure 1: Mission Planner.

### 4.1 Installing Mission Planner

The very first step is to install the mission planner software. It is known
as GCS or Ground control system. It can be downloaded form here: http://firmware.ardupilot.org/Tools/MissionPlanner/MissionPlanner-latest. msi (http://firmware.ardupilot.org/Tools/MissionPlanner/MissionPlanner-latest.msi) Note This link will automatically download the latest version, so if you want to download the previous versions than you can go to http: //firmware.ardupilot.org

After downloading the software go through the installation process. Follow the instructions to complete the setup process. The installation utility will automatically install any necessary software drivers. If you receive a DirectX installation error, please update your DirectX plug-in from the DirectX Download Center link is: http://www.microsoft.com/en-us/download/details.aspx?id=35. (http://www.microsoft.com/en-us/download/details.aspx?id=35)

If you receive the warning pictured in Fig 2, select Install this driver software anyway to continue.

4


Figure 2: Warning Screen.

An icon to open the Mission Planner is created according to your instructions during the installation.

### 4.2 Loading Firmware into APM 2.6

### 4.2.1 Connection

Connect controller to computer Once youve installed the Mission Planner onto your computer, connect the autopilot board to your computer using the micro USB cable as shown below. Use a direct USB port on your computer (not a USB hub).


Figure 3: APM USB Connection.

5

### 4.2.2 Connect to Mission Planner

Open the Mission Planner and select the COM port drop-down on the upperright corner of the screen (near the Connect button). Select AUTO or the specific port for your board (Arduino Mega 2560). Set the Baud rate to 115200 as shown. Dont hit Connect just yet.

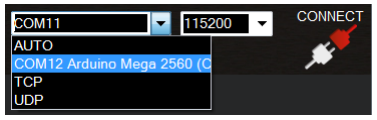
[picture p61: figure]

Figure 4: COM Port.

### 4.2.3 Install firmware

On the Mission Planners Initial Setup — Install Firmware screen select the appropriate icon that matches your frame (i.e. Quad, Hexa). Answer Yes when it asks you Are you sure?.


Figure 5: Install Firmware Screen.

Here you will see that the version shown is AC3.3.3 but if you want to use a previous version than you can select pick previous firmware and from

6

the dropdown you can select the required version in this case v3.2.1. If all goes well you will see some status appear on the bottom right including the words, erase..., program..., verify.. and Upload Done. The firmware has been succesfully uploaded to the board.

### 4.3 Calibrating the APM

Once you have installed the firmware and if the APM is not connected to the mission planner then click on the connect button on the top right corner. Once the board is connected

Click on Mandatory Hardware and you will see a dropdown with options like Frame Type, Acc Calibration, etc. Follow the steps in each option and go through the instructions and it should successfully calibrate the APM.

If you need any assistance on how to calibrate then you can check out this link: http://ardupilot.org/copter/docs/configuring-hardware.html and go through the step by step guide on whole calibration process

### 4.4 Testing

You can test the firmware is basically working by switching to the Mission Planner Flight Data screen and pressing the Connect button. The HUD should update as you tilt the board.

### 4.5 Troubleshooting

If Mission planner is unable to connect:

1. Check that the correct baud rate is used for the selected method (115200 on USB or 57600 on Radio/Telemetry)
2. If using a COM port on Windows, check that the connections COM port exists in the Windows Device Managers list of serial ports.
3. If using a USB port, try a different physical USB port

You should also ensure that the autopilot controller board has appropriate ArduPilot firwmare installed and has booted correctly (on APM there are useful LEDs which can tell you the state of the autopilot).

7

So, if you follow this tutorial properly you should be able to calibrate the APM successfully. You may face some errors like INS not calibrated, Compass/Gyro bad health, RC not calibrated, we suggest that you should go through the process once again and if the error persists then you can find about it’s troubleshooting on the net!

## 5 References

http://ardupilot.org/planner/docs/common-install-mission-planner.
html (http://ardupilot.org/planner/docs/common-install-mission-planner.html)

http://ardupilot.org/planner/docs/common-loading-firmware-onto-pixhawk. html (http://ardupilot.org/planner/docs/common-loading-firmware-onto-pixhawk.html)

http://ardupilot.org/planner/docs/common-connect-mission-planner-autopilot. html (http://ardupilot.org/planner/docs/common-connect-mission-planner-autopilot.html)

Everything mentioned above has been referred from the official documentation.

8

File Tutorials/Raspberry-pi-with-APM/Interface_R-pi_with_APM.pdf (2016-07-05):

## Interfacing Raspberry-pi with APM flight controller

Akshit Gandhi
Keyur Rakholiya

June 30, 2016

1

## Contents

1 Objective | 3
2 Prerequisites | 3
3 Hardware Requirement | 3
4 Procedure | 3
5 References | 9

2

## 1 Objective

Topic: Interfacing Raspberry-pi with APM(ARDUPILOT) flight controller APM is a flight controller which performs the stabilization of quadcopter by varying the signal to the motors based upon Radio control input. It has different flight modes which we can set from remote. It also supports different sensors like GPS ,Sonar etc. In this tutorial we will learn to how to setup a communication between the and APM flight controller, so that we can run/write our python scripts on R-PI and execute them on our drone. We will be going into details of each step.

## 2 Prerequisites

It’s better if you first go through the official documentation on ardupilot’s website on connecting R-PI with APM.[1], it will be beneficial also for this tutorial and also for later tutorials.

## 3 Hardware Requirement

Drone or Quadcopter, Raspberry pi, telemetry port connector for connecting APM to RPI and few jumpers(M-F).

## 4 Procedure

This tutorial explains how to connect and configure a Raspberry Pi (RPi) so that it is able to communicate with a APM flight controller using the MAVLink protocol[2] over a serial connection

3


Figure 1: Connection diagram.

The picture shown above is for pixhawk controller but the same connection works for APM also.

### 4.1 Connecting to RPi with an SSH/Telnet client

NOTE: These steps assume that you have already set-up your RPi so that it is running Raspbian.
To avoid the requirement to plug a keyboard, mouse and HDMI screen into your RPi it is convenient to be able to connect from your Desktop/Laptop computer to your RPi using an SSH/Telnet client such as PuTTY.
- Connect the RPi to your local network by one of the following methods:

– Connecting an Ethernet LAN cable from the RPi board to your Ethernet router, or

– Use a USB dongle to connect your RPi to the local wireless network, or

– Connect the Ethernet LAN cable between the RPi and your desktop/laptop computer. Open the control panels Network and Sharing Center, click on the network connection through which your desktop/laptop is connected to the internet, select properties and then in the sharing tab, select Allow other networks to connect through this computers Internet connection

- Determine the RPis IP address:

4

– If you have access to the RPis terminal screen (i.e.you have a screen, keyboard, mouse connected) you can use the /sbin/ifconfig command.


Figure 2: ip address on terminal.

– If your Ethernet router has a web interface it may show you the IP address of all connected devices

- Connect with Putty:

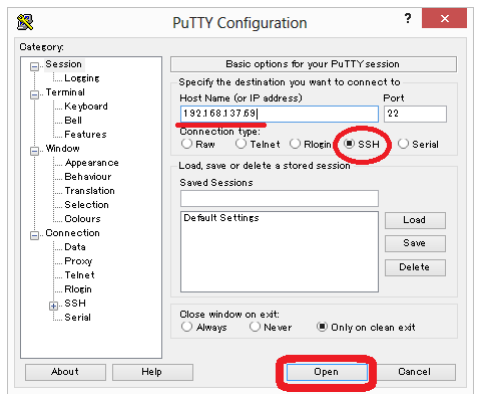
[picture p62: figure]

Figure 3: Connect screen with Putty.

If all goes well you should be presented with the regular login prompt to which you can enter the username/password which defaults to pi/raspberry

5

### 4.2 Install the required packages on the Raspberry Pi

Log into the RPi board (default username password is pi/raspberry) and check that its connection to the internet is working. If there’s some problem then troubleshooting guide can be found on the documentation site http: //ardupilot.org/dev/docs/raspberry-pi-via-mavlink.html

After the internet connection is confirmed to be working install these packages:

- sudo apt-get update
- sudo apt-get install screen python-wxgtk2.8 python-matplotlib pythonopencv python-pip python-numpy python-dev libxml2-dev libxslt-dev
- sudo pip install pymavlink
- sudo pip install mavproxy

### 4.3 Disable the OS control of the serial port

Use the Raspberry Pi configuration utility for this.

Type:

- sudo raspi-config
- And in the utility, select Advanced Options:

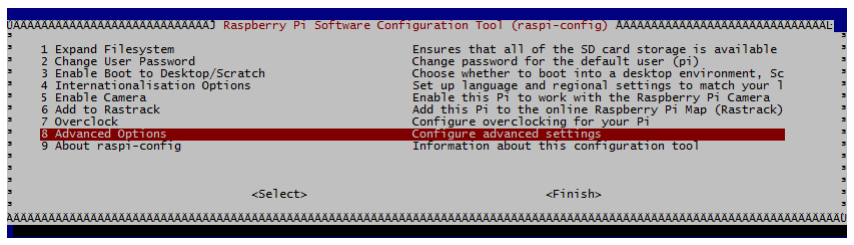
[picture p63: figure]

Figure 4: RasPiConfiguration Utility: Serial Settings: Advanced Options.

– And then Serial to disable OS use of the serial connection:

Reboot the Raspberry Pi when you are done.

6

### 4.4 Testing the connection

To test the RPi and APM are able to communicate with each other first ensure the RPi and APM are powered, then in a console on the RPi type:

- sudo -s
- mavproxy.py –master=/dev/ttyAMA0 –baudrate 57600 –aircraft My-Copter

raspberry pi’s default port is connected with console input/output. so use this port we have to disable it first. now we have connected our device via UART port ot R-Pi. so ”/dev/ttyAMA0” is a port for serial communication between R-pi and APM.

You configure BaudRate as bits per second. The transferred bits include the start bit, the data bits, the parity bit (if used), and the stop bits. However, only the data bits are stored.

The baud rate is the rate at which information is transferred in a communication channel. In the serial port context, ”9600 baud” means that the serial port is capable of transferring a maximum of 9600 bits per second. If the information unit is one baud (one bit), the bit rate and the baud rate are identical. If one baud is given as 10 bits, (for example, eight data bits plus two framing bits), the bit rate is still 9600 but the baud rate is 9600/10, or 960. You always configure BaudRate as bits per second. Therefore, in the previous example, set BaudRate to 9600.

Note: In the above command it’s MyCopter and My-Copter

- Once MAVProxy has started you should be able to type in the following command to display the ARMING CHECK parameters value

– param show ARMING CHECK

– param set ARMING CHECK 0

– arm throttle

∗ And then Serial to disable OS use of the serial connection:

7


Figure 5: Terminal screen.

NOTE: If you get an error about not being able to find log files or if this example otherwise doesnt run properly, make sure that you havent accidentally assigned these files to another username, such as Root.

8

Entering the following at the Linux command line will ensure that all files belong to the standard Pi login account: ∗ sudo chown -R pi /home/pi

### 4.5 Configure MAVProxy to always run

To setup MAVProxy to start whenever the RPi is restarted open a terminal window and edit the /etc/rc.local file, adding the following lines just before the final exit 0 line:

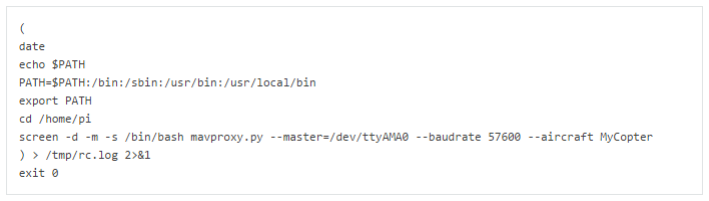
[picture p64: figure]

To open /etc/rc.local file type in sudo nano /etc/rc.local and type the code below and save it in the file

If you wish to connect to the MAVProxy application that has been automatically started you can log into the RPi and type: sudo screen -x

It is also worth noting that MAVProxy can do a lot more than just provide access to your APM. By writing python extension modules for MAVProxy you can add sophisticated autonomous behaviour to your vehicle. A MAVProxy module has access to all of the sensor information that your APM has, and can control all aspects of the flight.

## 5 References

[1]http://ardupilot.org/dev/docs/raspberry-pi-via-mavlink.html[2]http://qgroundcontrol.org/mavlink/start http://ardupilot.org/dev/docs/raspberry-pi-via-mavlink.html (http://ardupilot.org/dev/docs/raspberry-pi-via-mavlink.html)

Everything mentioned above bit by bit is from the official documentation.

9

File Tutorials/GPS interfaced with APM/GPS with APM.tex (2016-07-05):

%%%%%%%%%%%%%%%%%%%%%%%%%%%%%%%%%%%%%%%%%%%%%%%%%%%%%%%%%%%%%%%%%%%%%%%%%%%%%
%	e-Yantra, IIT-Bombay

%	Document Author: Saurav Shandilya
%	Date: 16-August,2012
%	Last Editted by: Saurav
%   Date Last updated: 31-05-2016 

%%%%%%%%%%%%%%%%%%%%%%%%%%%%%%%%%%%%%%%%%%%%%%%%%%%%%%%%%%%%%%%%%%%%%%%%%%%%%

\documentclass[11pt,a4paper]{article}
\usepackage{graphicx}
\usepackage{caption}
\usepackage{hyperref}
\usepackage{graphicx}
\title{Interfacing GPS with APM}
\author{Akshit Gandhi \\ Keyur Rakholiya}
\date{June 16, 2016}

\begin{document}
	\maketitle
	\newpage
	\tableofcontents
	\newpage
	\section{Tutorial Name}
	Interfacing GPS with APM
	\section{Prerequisites}
	Before reading this tutorial read about APM and read DATASHEET of your GPS module.
	\section{Hardware Requirement}
	\begin{center}
	
		\captionof{figure}{GPS}

	
		\captionof{figure}{APM 2.6 FLIGHT CONTROLLER}
	\end{center}
	\newpage
	\section{Software Requirement}

	MISSION PLANNER SOFTWARE 1.3.30

	\section{Theory and Description}
		connect the GPS to APM via GPS port which is given in APM.
		follow this image for connections.
		\begin{center}

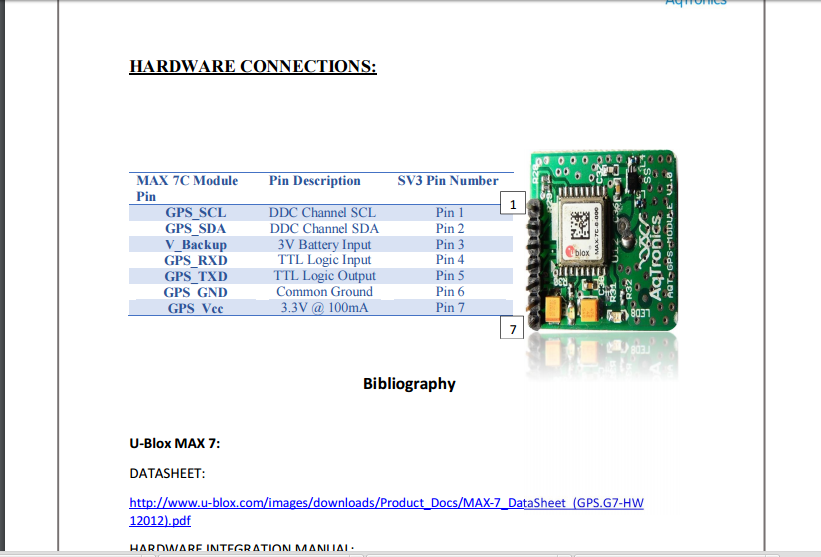
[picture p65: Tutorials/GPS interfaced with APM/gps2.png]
		
			\captionof{figure}{GPS module pin Diagram}
		
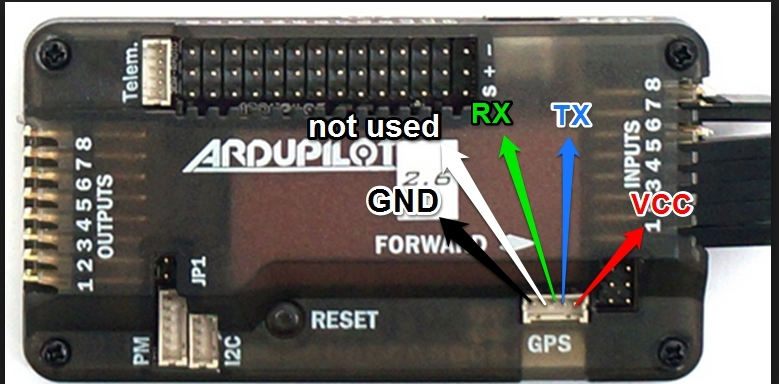
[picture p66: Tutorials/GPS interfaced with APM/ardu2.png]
		
			\captionof{figure}{GPS Pin on APM}
		\end{center}
		
		\vspace{1in}
		connect the module as shown in figure. connect APM with Mission planner and go to under open sky.
		for perfect gps location you GPS module should be under open sky. after 2 or 3 minutes GPS satellites will be connected to module. and you will find your Location on map in MISSION PLANNER software. you can also see no. of satellites connected to your gps module. \\
		
		you will also get value of longitude,latitude,altitude on terminal of mission planner software.\newline
		
		\begin{center}
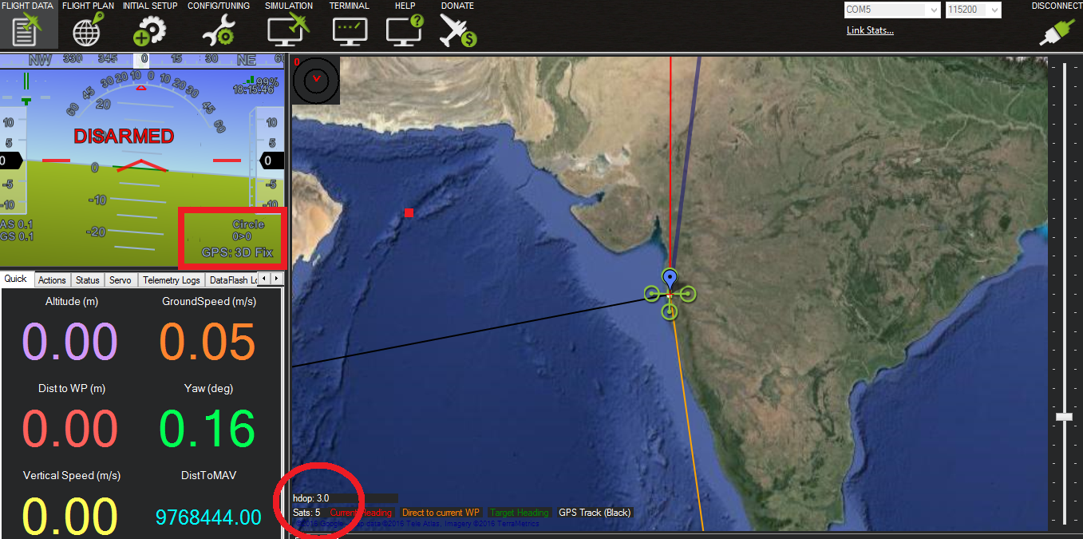
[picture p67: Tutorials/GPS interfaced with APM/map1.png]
		
		\captionof{figure}{current location}
		\end{center}
		\hspace{0.5in}
		as you can see in the figure. mission planner shows 3D fix and no. of satellites are 5.
		
		\newpage
		\hspace{0.5in}
		as you move from one place to another you will be tracked as you can see in image.
			\begin{center}
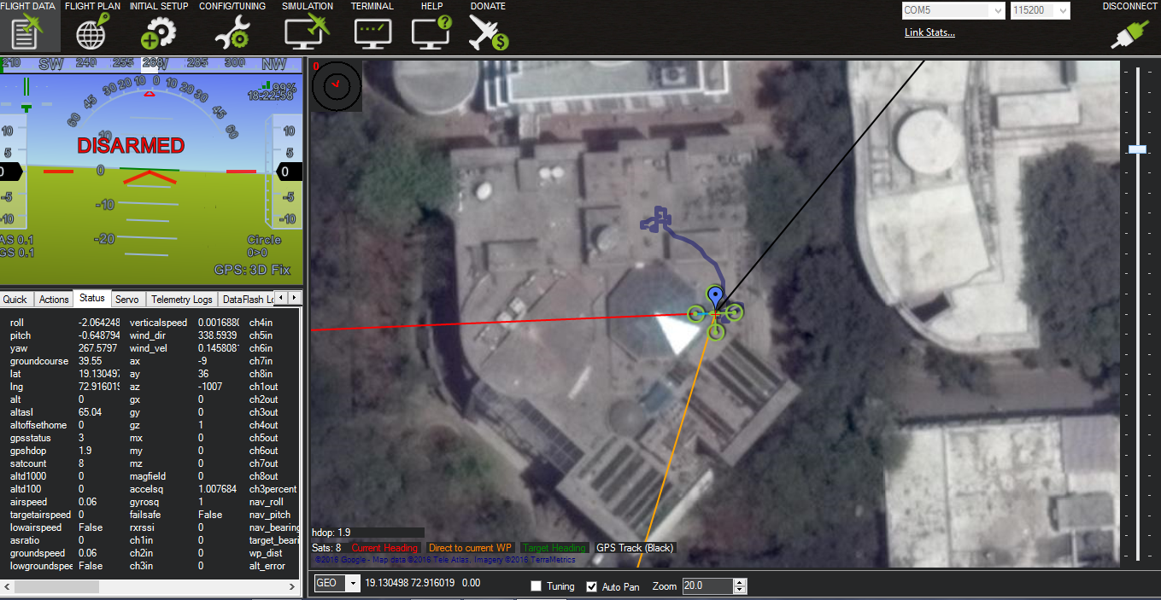
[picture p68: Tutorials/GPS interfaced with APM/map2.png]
				
				\captionof{figure}{closer look to location}
			\end{center}
	you can see  LAT , LON ,ALT and SATS on terminal.
		\begin{center}
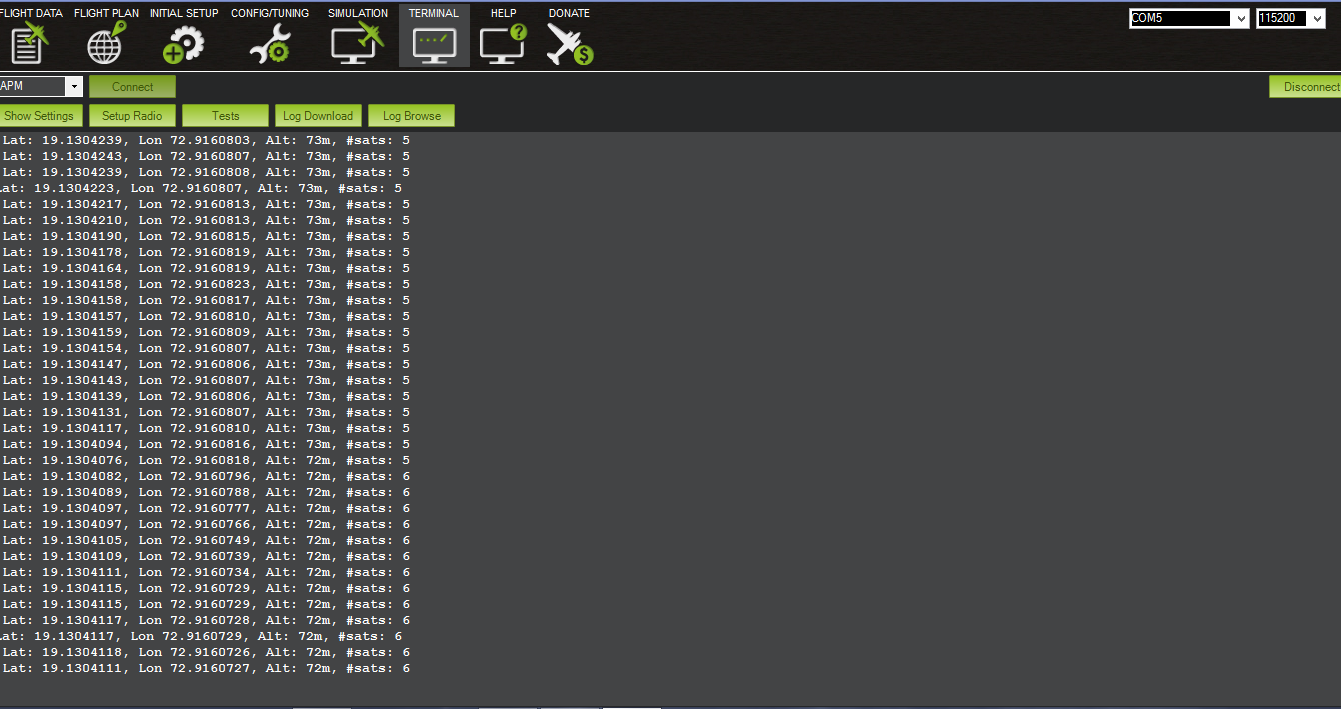
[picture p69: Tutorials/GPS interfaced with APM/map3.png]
			
			\captionof{figure}{DATA from terminal}
		\end{center}

	\section{References}
	\url{http://ardupilot.org/copter/docs/common-installing-3dr-ublox-gps-compass-module.html}
	\paragraph{•}
		 Our GPS datasheet.
\end{document}

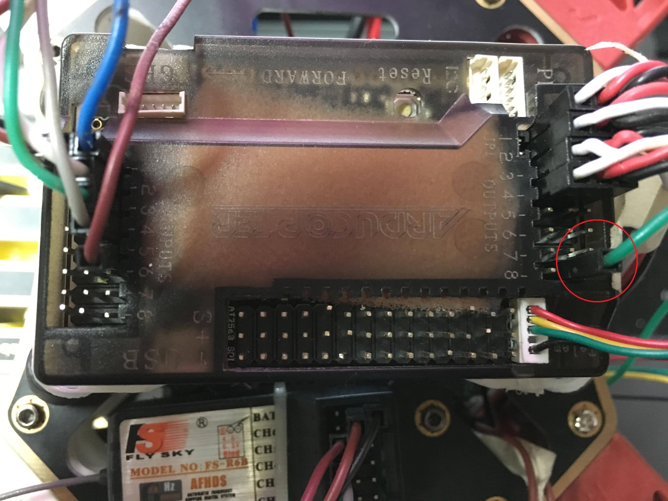
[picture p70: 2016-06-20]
Tutorials/Power Management System/Apm.jpeg

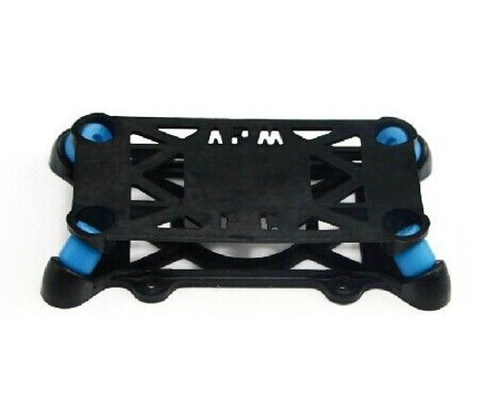
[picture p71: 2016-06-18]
Tutorials/assembly/vib.jpg

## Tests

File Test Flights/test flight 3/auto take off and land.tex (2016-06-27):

%%%%%%%%%%%%%%%%%%%%%%%%%%%%%%%%%%%%%%%%%%%%%%%%%%%%%%%%%%%%%%%%%%%%%%%%%%%%%
%	e-Yantra, IIT-Bombay

%	Document Author: keyur rakholiya and akshit gandhi
%	Date: 16-August,2012
%	Last Editted by: Saurav
%   Date Last updated: 31-05-2016 

%%%%%%%%%%%%%%%%%%%%%%%%%%%%%%%%%%%%%%%%%%%%%%%%%%%%%%%%%%%%%%%%%%%%%%%%%%%%%

\documentclass[11pt,a4paper]{article}
\usepackage{graphicx}
\usepackage{hyperref}
\usepackage{graphicx}
\title{AUTO TAKEOFF AND LANDING}
\author{keyur Rakholiya}
\date{\today}

\begin{document}
	\maketitle
	\newpage
	\tableofcontents
	\newpage
	\section{Tutorial Name}
	\hspace{0.5in}AUTO TAKEOFF AND AUTO LANDING

	\section{Theory and Description}
		we have connected R pi and Apm through UART. and we have written a code in python. so after running this code on r pi.drone will take off autonomously without any control. it will go up to hight of 2 m. then after 10 seconds it will go in LAND mode.\\
		you can see video on youtube. \\
		\\
		\url{https://www.youtube.com/watch?v=GHcQYoiWwgk}\\
		\\
		\\
		code is here:\\
		\\
		https://github.com/eYSIP-2016/Autonomous-Drone
		\newline

\end{document}

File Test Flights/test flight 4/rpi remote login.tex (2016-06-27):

%%%%%%%%%%%%%%%%%%%%%%%%%%%%%%%%%%%%%%%%%%%%%%%%%%%%%%%%%%%%%%%%%%%%%%%%%%%%%
%	e-Yantra, IIT-Bombay

%	Document Author: Saurav Shandilya
%	Date: 16-August,2012
%	Last Editted by: Saurav
%   Date Last updated: 31-05-2016 

%%%%%%%%%%%%%%%%%%%%%%%%%%%%%%%%%%%%%%%%%%%%%%%%%%%%%%%%%%%%%%%%%%%%%%%%%%%%%

\documentclass[11pt,a4paper]{article}

\usepackage{graphicx}
\title{Manual flight using Raspberry pi}
\author{keyur Rakholiya}
\author{akshit gandhi}
\date{\today}

\begin{document}
	\maketitle
	\newpage
	\tableofcontents
	\newpage
	\section{Tutorial Name}
		Manual Flight using Raspberry pi

	\section{Hardware Requirement}
		Drone with APM2.6 Controller\\
		Raspberry Pi B+

	\section{Software Requirement}
		Mission planner software\\
		Moboxterm for Raspberry pi
	\section{Theory and Description}
		we have connected R pi to Apm through UARTs. we have also connect GPIO of Rpi to INPUT of APM.\\
		so we have two type of communication.\\
		1)through UARTS\\
		2)through GPIO(one way communication)\\
		\\
		we actually get feed back from APM through UART port. we are generating PWM Signal through R pi's GPIO.
		so we have removed remote(RC control) input from APM.
	\section{Experiment}
		now, we have one indoor flight in which ,we can control drone through our key board keys.\\
		we have noticed that its very stable and more accurate then remote control.
	\section{Exercise}
		whole python code for raspberry pi is given on github.\\
		\url{https://github.com/eYSIP-2016/Autonomous-Drone}

\end{document}

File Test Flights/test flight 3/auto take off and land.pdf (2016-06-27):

## AUTO TAKEOFF AND LANDING

keyur Rakholiya

June 27, 2016

1

## Contents

1 Tutorial Name | 3
2 Theory and Description | 3

2

## 1 Tutorial Name

AUTO TAKEOFF AND AUTO LANDING

## 2 Theory and Description

we have connected R pi and Apm through UART. and we have written a code in python. so after running this code on r pi.drone will take off autonomously without any control. it will go up to hight of 2 m. then after 10 seconds it will go in LAND mode.
you can see video on youtube.

https://www.youtube.com/watch?v=GHcQYoiWwgk

code is here:

https://github.com/eYSIP-2016/Autonomous-Drone

3

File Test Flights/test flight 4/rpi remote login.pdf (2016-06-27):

## Manual flight using Raspberry pi

akshit gandhi

June 27, 2016

1

## Contents

1 Tutorial Name | 3
2 Hardware Requirement | 3
3 Software Requirement | 3
4 Theory and Description | 3
5 Experiment | 3
6 Exercise | 3

2

## 1 Tutorial Name

Manual Flight using Raspberry pi

## 2 Hardware Requirement

Drone with APM2.6 Controller Raspberry Pi B+

## 3 Software Requirement

Mission planner software
Moboxterm for Raspberry pi

## 4 Theory and Description

we have connected R pi to Apm through UARTs. we have also connect GPIO of Rpi to INPUT of APM.
so we have two type of communication.
1)through UARTS
2)through GPIO(one way communication)

we actually get feed back from APM through UART port. we are generating PWM Signal through R pi’s GPIO. so we have removed remote(RC control) input from APM.

## 5 Experiment

now, we have one indoor flight in which ,we can control drone through our key board keys.
we have noticed that its very stable and more accurate then remote control.

## 6 Exercise

whole python code for raspberry pi is given on github. https://github.com/eYSIP-2016/Autonomous-Drone

3

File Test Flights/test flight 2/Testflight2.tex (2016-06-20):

%%%%%%%%%%%%%%%%%%%%%%%%%%%%%%%%%%%%%%%%%%%%%%%%%%%%%%%%%%%%%%%%%%%%%%%%%%%%%
%	e-Yantra, IIT-Bombay

%	Document Author: Saurav Shandilya
%	Date: 16-August,2012
%	Last Editted by: Saurav
%   Date Last updated: 31-05-2016 

%%%%%%%%%%%%%%%%%%%%%%%%%%%%%%%%%%%%%%%%%%%%%%%%%%%%%%%%%%%%%%%%%%%%%%%%%%%%%

\documentclass[11pt,a4paper]{article}
\usepackage{graphicx}
\usepackage{hyperref}
\usepackage{graphicx}
\title{Drone -Test Flight 2}
\author{keyur Rakholiya}
\author{Akshit Gandhi}
\date{\today}

\begin{document}
	\maketitle
	\newpage
	\tableofcontents
	\newpage
	\section{Tutorial Name}
	Test Flight 2

	\section{Theory and Description}
		when we went for test flight 2. everything was alright. we had checked all the soft parameters of the Drone. we have also took care about atmosphere. but sometimes very small mistakes leads to crash. we have not given too much attention to the hardware. so during the flight at the height of 6 meter ,oe of the propeller slipped out. and flight got crashed.
		as you can see in video...
		
		\url{https://youtu.be/dcHOmJOeLvU}
		\newline
		
	\section{References}
		\paragraph\url{https://github.com/eYSIP-2016/Autonomous-Drone}
	
\end{document}

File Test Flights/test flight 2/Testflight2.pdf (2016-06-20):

## Drone -Test Flight 2

Akshit Gandhi

June 20, 2016

1

## Contents

2

## 1 Tutorial Name

Test Flight 2

## 2 Theory and Description

when we went for test flight 2. everything was alright. we had checked all the soft parameters of the Drone. we have also took care about atmosphere. but sometimes very small mistakes leads to crash. we have not given too much attention to the hardware. so during the flight at the height of 6 meter ,oe of the propeller slipped out. and flight got crashed. as you can see in video...
https://youtu.be/dcHOmJOeLvU

## 3 References

https://github.com/eYSIP-2016/Autonomous-Drone

3

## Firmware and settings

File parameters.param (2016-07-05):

#NOTE: sonar working
ACRO_BAL_PITCH,1
ACRO_BAL_ROLL,1
ACRO_EXPO,0.3
ACRO_RP_P,4.5
ACRO_TRAINER,2
ACRO_YAW_P,4.5
AHRS_COMP_BETA,0.1
AHRS_GPS_GAIN,1
AHRS_GPS_MINSATS,6
AHRS_GPS_USE,1
AHRS_ORIENTATION,0
AHRS_RP_P,0.1
AHRS_TRIM_X,-0.03883692
AHRS_TRIM_Y,-0.0007720405
AHRS_TRIM_Z,0
AHRS_WIND_MAX,0
AHRS_YAW_P,0.1
ANGLE_MAX,4500
ARMING_CHECK,0
ATC_ACCEL_RP_MAX,0
ATC_ACCEL_Y_MAX,0
ATC_RATE_FF_ENAB,0
ATC_RATE_RP_MAX,18000
ATC_RATE_Y_MAX,9000
ATC_SLEW_YAW,1000
BAROGLTCH_ACCEL,1500
BAROGLTCH_DIST,500
BAROGLTCH_ENABLE,1
BATT_AMP_OFFSET,0
BATT_AMP_PERVOLT,17
BATT_CAPACITY,5000
BATT_CURR_PIN,3
BATT_MONITOR,4
BATT_VOLT_MULT,10.1
BATT_VOLT_PIN,2
BATT_VOLT2_MULT,1
BATT_VOLT2_PIN,-1
CAM_DURATION,10
CAM_SERVO_OFF,1100
CAM_SERVO_ON,1300
CAM_TRIGG_DIST,0
CAM_TRIGG_TYPE,0
CH7_OPT,18
CH8_OPT,0
CIRCLE_RADIUS,1000
CIRCLE_RATE,20
COMPASS_AUTODEC,0
COMPASS_DEC,0
COMPASS_EXTERNAL,0
COMPASS_LEARN,0
COMPASS_MOT_X,0
COMPASS_MOT_Y,0
COMPASS_MOT_Z,0
COMPASS_MOTCT,0
COMPASS_OFS_X,0
COMPASS_OFS_Y,0
COMPASS_OFS_Z,0
COMPASS_ORIENT,0
COMPASS_USE,1
DCM_CHECK_THRESH,0.8
EKF_CHECK_THRESH,0.8
ESC,0
FENCE_ACTION,1
FENCE_ALT_MAX,10
FENCE_ENABLE,0
FENCE_MARGIN,2
FENCE_RADIUS,300
FENCE_TYPE,1
FLOW_ENABLE,0
FLTMODE1,0
FLTMODE2,0
FLTMODE3,2
FLTMODE4,2
FLTMODE5,9
FLTMODE6,9
FRAME,1
FS_BATT_ENABLE,1
FS_BATT_MAH,0
FS_BATT_VOLTAGE,10
FS_GCS_ENABLE,0
FS_GPS_ENABLE,1
FS_THR_ENABLE,0
FS_THR_VALUE,975
GND_ABS_PRESS,99715.17
GND_ALT_OFFSET,0
GND_TEMP,36.27721
GPS_HDOP_GOOD,230
GPS_NAVFILTER,8
GPS_TYPE,1
GPSGLITCH_ACCEL,1000
GPSGLITCH_ENABLE,1
GPSGLITCH_RADIUS,200
HLD_LAT_P,1
INAV_TC_XY,2.5
INAV_TC_Z,5
INS_ACCOFFS_X,-0.07023904
INS_ACCOFFS_Y,0.05350644
INS_ACCOFFS_Z,0.843851
INS_ACCSCAL_X,1.012507
INS_ACCSCAL_Y,0.9912577
INS_ACCSCAL_Z,1.000847
INS_GYROFFS_X,-0.05325354
INS_GYROFFS_Y,0.0108444
INS_GYROFFS_Z,0.05727629
INS_MPU6K_FILTER,0
INS_PRODUCT_ID,0
LAND_REPOSITION,1
LAND_SPEED,50
LOG_BITMASK,26622
LOITER_LAT_D,0
LOITER_LAT_I,0.5
LOITER_LAT_IMAX,1000
LOITER_LAT_P,1
LOITER_LON_D,0
LOITER_LON_I,0.5
LOITER_LON_IMAX,1000
LOITER_LON_P,1
MAG_ENABLE,0
MIS_RESTART,0
MIS_TOTAL,7
MNT_ANGMAX_PAN,4500
MNT_ANGMAX_ROL,4500
MNT_ANGMAX_TIL,0
MNT_ANGMIN_PAN,-4500
MNT_ANGMIN_ROL,-4500
MNT_ANGMIN_TIL,-9000
MNT_CONTROL_X,0
MNT_CONTROL_Y,0
MNT_CONTROL_Z,0
MNT_JSTICK_SPD,0
MNT_MODE,3
MNT_NEUTRAL_X,0
MNT_NEUTRAL_Y,0
MNT_NEUTRAL_Z,0
MNT_RC_IN_PAN,0
MNT_RC_IN_ROLL,0
MNT_RC_IN_TILT,6
MNT_RETRACT_X,0
MNT_RETRACT_Y,0
MNT_RETRACT_Z,0
MNT_STAB_PAN,0
MNT_STAB_ROLL,0
MNT_STAB_TILT,0
MOT_SPIN_ARMED,70
MOT_TCRV_ENABLE,1
MOT_TCRV_MAXPCT,93
MOT_TCRV_MIDPCT,52
OF_PIT_D,0.12
OF_PIT_I,0.5
OF_PIT_IMAX,100
OF_PIT_P,2.5
OF_RLL_D,0.12
OF_RLL_I,0.5
OF_RLL_IMAX,100
OF_RLL_P,2.5
PHLD_BRAKE_ANGLE,3000
PHLD_BRAKE_RATE,8
PILOT_ACCEL_Z,250
PILOT_VELZ_MAX,250
POSCON_THR_HOVER,512
RATE_PIT_D,0.0055
RATE_PIT_I,0.07999999
RATE_PIT_IMAX,1000
RATE_PIT_P,0.07999999
RATE_RLL_D,0.003
RATE_RLL_I,0.08499999
RATE_RLL_IMAX,1000
RATE_RLL_P,0.08499999
RATE_YAW_D,0.003
RATE_YAW_I,0.02
RATE_YAW_IMAX,1000
RATE_YAW_P,0.17
RC_FEEL_RP,100
RC_SPEED,490
RC1_DZ,30
RC1_MAX,1900
RC1_MIN,1100
RC1_REV,1
RC1_TRIM,1534
RC10_DZ,0
RC10_FUNCTION,0
RC10_MAX,1900
RC10_MIN,1100
RC10_REV,1
RC10_TRIM,1500
RC11_DZ,0
RC11_FUNCTION,0
RC11_MAX,1900
RC11_MIN,1100
RC11_REV,1
RC11_TRIM,1500
RC2_DZ,30
RC2_MAX,1900
RC2_MIN,1100
RC2_REV,-1
RC2_TRIM,1488
RC3_DZ,30
RC3_MAX,2000
RC3_MIN,1100
RC3_REV,1
RC3_TRIM,1214
RC4_DZ,40
RC4_MAX,1900
RC4_MIN,1100
RC4_REV,1
RC4_TRIM,1515
RC5_DZ,0
RC5_FUNCTION,0
RC5_MAX,1515
RC5_MIN,1002
RC5_REV,1
RC5_TRIM,1005
RC6_DZ,0
RC6_FUNCTION,0
RC6_MAX,1499
RC6_MIN,1498
RC6_REV,1
RC6_TRIM,1498
RC7_DZ,0
RC7_FUNCTION,0
RC7_MAX,1499
RC7_MIN,1498
RC7_REV,1
RC7_TRIM,1498
RC8_DZ,0
RC8_FUNCTION,0
RC8_MAX,1499
RC8_MIN,1498
RC8_REV,1
RC8_TRIM,1499
RCMAP_PITCH,2
RCMAP_ROLL,1
RCMAP_THROTTLE,3
RCMAP_YAW,4
RELAY_PIN,13
RELAY_PIN2,-1
RNGFND_FUNCTION,0
RNGFND_GAIN,0.02
RNGFND_MAX_CM,700
RNGFND_MIN_CM,20
RNGFND_OFFSET,0
RNGFND_PIN,0
RNGFND_RMETRIC,1
RNGFND_SCALING,2.5
RNGFND_SETTLE_MS,1
RNGFND_STOP_PIN,-1
RNGFND_TYPE,1
RSSI_PIN,-1
RSSI_RANGE,5
RTL_ALT,1500
RTL_ALT_FINAL,0
RTL_LOIT_TIME,5000
SCHED_DEBUG,0
SERIAL0_BAUD,115
SERIAL1_BAUD,57
SIMPLE,0
SR0_EXT_STAT,2
SR0_EXTRA1,10
SR0_EXTRA2,10
SR0_EXTRA3,2
SR0_PARAMS,10
SR0_POSITION,3
SR0_RAW_CTRL,2
SR0_RAW_SENS,2
SR0_RC_CHAN,2
SR1_EXT_STAT,2
SR1_EXTRA1,2
SR1_EXTRA2,2
SR1_EXTRA3,2
SR1_PARAMS,0
SR1_POSITION,2
SR1_RAW_CTRL,2
SR1_RAW_SENS,2
SR1_RC_CHAN,2
STB_PIT_P,4.875
STB_RLL_P,4.875
STB_YAW_P,4
SUPER_SIMPLE,0
SYSID_MYGCS,255
SYSID_SW_MREV,120
SYSID_SW_TYPE,10
SYSID_THISMAV,1
TELEM_DELAY,0
THR_ACCEL_D,0
THR_ACCEL_I,1
THR_ACCEL_IMAX,800
THR_ACCEL_P,0.5
THR_ALT_P,1
THR_DZ,100
THR_MAX,1000
THR_MID,510
THR_MIN,200
THR_RATE_P,6
TRIM_THROTTLE,512
TUNE,0
TUNE_HIGH,1000
TUNE_LOW,0
WP_YAW_BEHAVIOR,2
WPNAV_ACCEL,100
WPNAV_ACCEL_Z,100
WPNAV_LOIT_JERK,1000
WPNAV_LOIT_SPEED,1000
WPNAV_RADIUS,200
WPNAV_SPEED,500
WPNAV_SPEED_DN,150
WPNAV_SPEED_UP,250

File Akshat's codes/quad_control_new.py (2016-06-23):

import cv2
import numpy as np
from RPIO import PWM
import time
import io
import picamera
import picamera.array

# initialize servo objects with PWM function
roll = PWM.Servo()
pitch = PWM.Servo()
throttle = PWM.Servo()
yaw = PWM.Servo()
aux = PWM.Servo()

# start PWM on servo specific GPIO no, this is not the pin no but it is the GPIO no 
roll.set_servo(17,1520)# pin 11
pitch.set_servo(18,1520)# pin 12
throttle.set_servo(27,1100)# pin 13, pin 14 is Ground
yaw.set_servo(22,1520)# pin 15
aux.set_servo(23,1010)# pin 16

# assign global min and max values
th_min = 1100
th_max = 2400
r_min = 1100
r_max = 1900
p_min = 1100
p_max = 1900
y_min = 1100
y_max = 1900
a_min = 980
a_max = 2300
th = 1100
r = 1520
p = 1520
y = 1520
a = False
th1 = 0
bot_in_bounds = False

# initialize picamera objects
camera=picamera.PiCamera()
camera.resolution = (160,120)

stream= io.BytesIO()

try:
    while True:
        string = raw_input ('Enter Command: ')
        word = string.split()
        word1 = word[0]
        
        if word1 == 'ARM':
	    th = 1100
            throttle.set_servo(27,th)
            time.sleep(1)
            yaw.set_servo(22,1100)
            time.sleep(1)
            yaw.set_servo(22,1520)
            time.sleep(1)
            print 'System is armed'
            continue

        elif word1 == 'FLY':

            # mapping for MANUAL MODE
            if word[1] == 'MANUAL':
                print 'Flight control: MANUAL'

                try:
                    while True:
                        camera.capture(stream, format="bgr", use_video_port=True)
                        frame = np.fromstring(stream.getvalue(), dtype=np.uint8)
                        stream.seek(0)
                        frame= stream.array
                        cv2.imshow('frame',frame)

                        k = cv2.waitKey(1)

                        # mapping TH = UP
                        if (k & 0xFF) == ord('w'):
                            th = th + 10
                            if (th < th_min):
                                throttle.set_servo(27,1100)
                                th = 1100
                            elif (th > th_max):
                                throttle.set_servo(27,2400)
                                th = 2400
                            elif (th > th_min & th < th_max):
                                throttle.set_servo(27,th)
                            print 'TH: ' + str(th)
                            continue

                        # mapping TH = DOWN
                        if (k & 0xFF) == ord('s'):
                            th = th - 10
                            if (th < th_min):
                                throttle.set_servo(27,1100)
                                th = 1100
                            elif (th > th_max):
                                throttle.set_servo(27,2400)
                                th = 2400
                            elif (th > th_min & th < th_max):
                                throttle.set_servo(27,th)
                            print 'TH: ' + str(th)
                            continue

                        # mapping YA = LEFT
                        if (k & 0xFF) == ord('a'):
                            y = y - 10
                            if (y < y_min):
                                yaw.set_servo(22,1100)
                                y = 1100
                            elif (y > y_max):
                                yaw.set_servo(22,1900)
                                y = 1900
                            elif (y > y_min & y < y_max):
                                yaw.set_servo(22,y)
                            print 'YA: ' + str(y)
                            continue

                        # mapping YA = RIGHT
                        if (k & 0xFF) == ord('d'):
                            y = y + 10
                            if (y < y_min):
                                yaw.set_servo(22,1100)
                                y = 1100
                            elif (y > y_max):
                                yaw.set_servo(22,1900)
                                y = 1900
                            elif (y > y_min & y < y_max):
                                yaw.set_servo(22,y)
                            print 'YA: ' + str(y)
                            continue

                        # mapping PI = UP
                        elif (k & 0xFF) == ord('8'):
                            p = p + 10
                            if (p < p_min):
                                pitch.set_servo(18,1100)
                                p = 1100
                            elif (p > p_max):
                                pitch.set_servo(18,1900)
                                p = 1900
                            elif (p > p_min & p < p_max):
                                pitch.set_servo(18,p)
                            print 'PI: ' + str(p)
                            continue
            
                        # mapping PI = DOWN
                        if (k & 0xFF) == ord('2'):
                            p = p - 10
                            if (p < p_min):
                                pitch.set_servo(18,1100)
                                p = 1100
                            elif (p > p_max):
                                pitch.set_servo(18,1900)
                                p = 1900
                            elif (p > p_min & p < p_max):
                                pitch.set_servo(18,p)
                            print 'PI: ' + str(p)
                            continue

                        # mapping RO = LEFT
                        if (k & 0xFF) == ord('4'):
                            r = r - 10
                            if (r < r_min):
                                roll.set_servo(17,1100)
                                r = 1100
                            elif (r > r_max):
                                roll.set_servo(17,1900)
                                r = 1900
                            elif (r > r_min & r < r_max):
                                roll.set_servo(17,r)
                            print 'RO: ' + str(r)
                            continue

                        # mapping RO = RIGHT
                        if (k & 0xFF) == ord('6'):
                            r = r + 10
                            if (r < r_min):
                                roll.set_servo(17,1100)
                                r = 1100
                            elif (r > r_max):
                                roll.set_servo(17,1900)
                                r = 1900
                            elif (r > r_min & r < r_max):
                                roll.set_servo(17,r)
                            print 'RO: ' + str(r)
                            continue
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

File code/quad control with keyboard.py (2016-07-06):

##########################################################################################################################
# Project : Autonomous Drone												#
# Hardware: Raspberry pi ,Arducopter , laptop or desktop ,ultrasonic sensor HC-SR04					#
#	  : Arducopter(APM2.6)												#
# Author  : Keyur Rakholiya												#
# Author  : Akshit Gandhi												#
#															#
# by using this code, quadcopter can controlled by using laptop keyboard. we can also change the different modes also   #												#
#															#
# Requrinment: Refer Tutorial Folder											#
#########################################################################################################################
from dronekit import connect, VehicleMode ,LocationGlobalRelative
import time
import getch
from RPIO import PWM


print "connecting to vehicle...."
vehicle = connect('/dev/ttyAMA0', baud = 57600)
print "connected"

#changing vehicle mode to stabilize
print "\nSet Vehicle.mode = (currently: %s)" % vehicle.mode.name
while not vehicle.mode=='STABILIZE':
    vehicle.mode = VehicleMode('STABILIZE')
    vehicle.flush()

print "vehicle mode: %s" % vehicle.mode

# ARMING the vehicle
vehicle.armed = True
while not vehicle.armed:
    vehicle.armed = True
    vehicle.flush()
    print " trying to change mode and arming ..."
    time.sleep(1)

print "its armed"

# initialize servo objects with PWM function
roll = PWM.Servo()
pitch = PWM.Servo()
throttle = PWM.Servo()
yaw = PWM.Servo()
mode = PWM.Servo()

# start PWM on servo specific GPIO no, this is not the pin no but it is the GPIO no 
roll.set_servo(17,1520)# pin 11
pitch.set_servo(18,1520)# pin 12
throttle.set_servo(27,1100)# pin 13, pin 14 is Ground
yaw.set_servo(22,1520)# pin 15
mode.set_servo(26,1200)# pin 37
# assign global min and max values
th_min = 1100
th_max = 2000
r_min = 1100
r_max = 1900
p_min = 1100
p_max = 1900
y_min = 1100
y_max = 1900
a_min = 980
a_max = 2300
th =1100
r = 1520
p = 1520
y = 1520
a = False
flag = 0

#print "\nSet Vehicle.mode =  (currently: %s)" % vehicle.mode.name

print "Taking off!"
print "controll drone from keyboard"




try:
    while True:
# waiting for key strokes
        key = getch.getch()
        if key == 'w':
            
            th = th + 10
            if (th < th_min):
                th = 1100
                throttle.set_servo(27,th)
            elif (th > th_max):
                th = 2000
                throttle.set_servo(27,th)
            else: 
                throttle.set_servo(27,th)
            print 'th :' + str(th)
            
        elif key == 's':
            th = th - 10
            if (th < th_min):
                th = 1100
                throttle.set_servo(27,th)
            elif (th > th_max):
                th = 2000
                throttle.set_servo(27,th)
            else:
                throttle.set_servo(27,th)
            print 'th :' + str(th)

            #yaw left
        elif key == 'a':
            yaw.set_servo(22,1350)
	    print "yaw left"
            time.sleep(0.3)
            yaw.set_servo(22,1500)

        #yaw right
        elif key == 'd':
            yaw.set_servo(22,1650)
	    print "yaw right"
            time.sleep(0.3)
            yaw.set_servo(22,1500)

        #roll left
        elif key == '4':
            roll.set_servo(17,1350)
	    print "roll left"
            time.sleep(0.3)
            roll.set_servo(17,1500)

        #roll right
        elif key == '6':
            roll.set_servo(17,1650)
	    print "roll right"
            time.sleep(0.3)
            roll.set_servo(17,1500)
            
        #pitch forward
        elif key == '8':
            pitch.set_servo(18,1650)
	    print "pitch forward"
            time.sleep(0.3)
            pitch.set_servo(18,1500)
	#pitch back
	elif key == '2':
		pitch.set_servo(18,1350)
		print "pitch back"
		time.sleep(0.3)
		pitch.set_servo(18,1500)

        #atlitude hold
	elif key == 'h':
		mode.set_servo(26,1550)
		time.sleep(0.5)
		print " mode is %s" % vehicle.mode.name
		
      
	#land mode
	elif key == 'l':
		mode.set_servo(26,1800)
		time.sleep(0.5)
		print " mode is %s " % vehicle.mode.name
	#stabilize mode
	elif key =='5' and th<1200:
                mode.set_servo(26,1200)
                time.sleep(0.5)
                print "mode is %s" % vehicle.mode.name
                
except KeyboardInterrupt:
	throttle.set_servo(27,1100)
	while vehicle.armed:
		vehicle.armed = False
	        print "disarming"
		time.sleep(1)
		vehicle.flush()
print "DISARMED"
vehicle.close()

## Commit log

2016-06-08 added document about assembly
2016-06-18 Added Calibration and Rpi Interfacing Tutorials
2016-06-20 Added Power Management Tutorial
2016-06-22 Add 3D printing files
    [1.stl, 2.stl, Flamewheel_Arm_GPS_MastHolder.stl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]
2016-07-05 minor changes done
    [parameters.param]
2016-07-05 added 3D cage design
    [part1.stl, part2.stl]
2016-07-05 added ultrasonic sensor tutorial
2016-07-05 Update Autonomus take off and landing.py
2016-07-06 added ultrasonic sensor datasheet
2016-07-06 modified pin diagram in Ultrasonic
